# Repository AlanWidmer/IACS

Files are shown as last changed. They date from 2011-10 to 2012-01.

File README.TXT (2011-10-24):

The project is a fork of the shop.23b.org 'open access controller'. For the Jigsaw Renaissance space in the Inscape building we need to make some changes and additions.
The door controller will use the wireless ethernet infrastructure to pull a file that contains the list of valid keys from a server.

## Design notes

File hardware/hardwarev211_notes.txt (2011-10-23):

Open Access Control Notes
Updated 4/3/2011

Relay pins:
6,7,8,9

I2C for clock:
A4 (SDA)
A5 (SCL)
`
Analog pins (for alarm):
A0,A1,A2,A3

Reader inputs
Reader 1: 2,3
Reader 2: 4,5

Ethernet shield:
10,11,12,13

Changes sicne v2.00:
1.  Added additional TVS diode on the +5V rail
2.  Adjusted board layout so that insulator not needed under voltage regulator
3.  Tidied up silkscreen on top and bottom layers

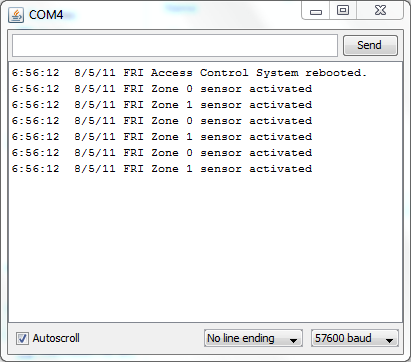
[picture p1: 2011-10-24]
Images/Running.PNG

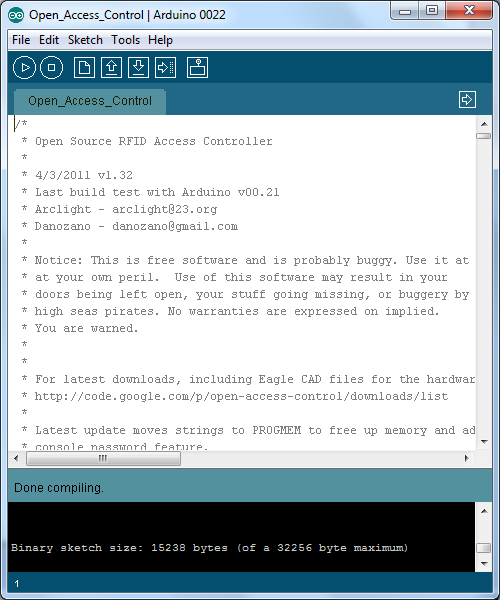
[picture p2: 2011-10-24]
Images/compiled.PNG

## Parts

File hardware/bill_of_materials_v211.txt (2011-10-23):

Partlist exported from H:/apps/eagle/projects/RFID/RFID_board_v200.sch at 1/20/2011 10:33:13 PM

Part    Value               Device               Package            Description                                                                                  DIGIKEY       MOUSER     
5VOUT                       W237-102             W237-102           WAGO SCREW CLAMP                                                                                           651-1935161
12VIN                       W237-102             W237-102           WAGO SCREW CLAMP                                                                                           651-1935161
12VOUTA                     W237-102             W237-102           WAGO SCREW CLAMP                                                                                           651-1935161
12VOUTB                     W237-102             W237-102           WAGO SCREW CLAMP                                                                                           651-1935161
BAT1                        BATTERY20PTH         BATTCOM_20MM_PTH   Battery Holders                                                                                            122-2420-GR
C1      100uF               CPOL-USE3.5-8        E3,5-8             POLARIZED CAPACITOR, American symbol                                                                                  
C2      0.1uF               C-US050-025X075      C050-025X075       CAPACITOR, American symbol                                                                                            
C3      330uF               CPOL-USE3.5-8        E3,5-8             POLARIZED CAPACITOR, American symbol                                                                                  
D1      1N5819              1N5819-B             DO41-7.6           1.0A SCHOTTKY BARRIER RECTIFIER                                                                                       
D2      15KE18A             15KE18A              DO201-15           TVS Diode, 18V                                                                                                         
D3	15KE6.8A	    15KE6.8A				    TVS Diode, 6.8V
D5      1N4004              1N4004               DO41-10            DIODE                                                                                                                 
D6      1N4004              1N4004               DO41-10            DIODE                                                                                                                 
D7      1N4004              1N4004               DO41-10            DIODE                                                                                                                 
D8      1N4004              1N4004               DO41-10            DIODE                                                                                                                 
D9      1N4004              1N4004               DO41-10            DIODE                                                                                                                 
D10     1N4004              1N4004               DO41-10            DIODE                                                                                                                 
D11     1N4004              1N4004               DO41-10            DIODE                                                                                                                 
D12     1N4004              1N4004               DO41-10            DIODE                                                                                                                 
D13     5A                  DIODE-P6-15          P6-15              DIODE                                                                                                                 
F1      2A                  5X20MMCLIP           SHK20Q             FUSE HOLDER Littelfuse 01110506H 5x20mm clips. Mouser part #576-01110506H                    F044-ND                  
F4      5A                  5X20MMCLIP           SHK20Q             FUSE HOLDER Littelfuse 01110506H 5x20mm clips. Mouser part #576-01110506H                    F044-ND                  
F6      2A                  5X20MMCLIP           SHK20Q             FUSE HOLDER Littelfuse 01110506H 5x20mm clips. Mouser part #576-01110506H                    F044-ND                  
F7      0.5A                5X20MMCLIP           SHK20Q             FUSE HOLDER Littelfuse 01110506H 5x20mm clips. Mouser part #576-01110506H                    F044-ND                  
IC1     DS1307              DS1307               DIL08              DS1307                                                                                       DS1307+-ND    700-DS1307 
IC5     ULN2003             ULN2003AN            DIL16              DRIVER ARRAY                                                                                                          
K0      GL5E-12V            ZNS5106              ZN5                Miniature Power PCB Relay SCHRACK                                                            Z1012-ND                 
K1      GL5E-12V            ZNS5106              ZN5                Miniature Power PCB Relay SCHRACK                                                            Z1012-ND                         
K2      GL5E-12V            ZNS5106              ZN5                Miniature Power PCB Relay SCHRACK                                                            Z1012-ND                 
K3      GL5E-12V            ZNS5106              ZN5                Miniature Power PCB Relay SCHRACK                                                            Z1012-ND                 
LED1    RED                 LED5MM               LED5MM             LED                                                                                                                   
LED2    RED                 LED5MM               LED5MM             LED                                                                                                                   
LED3    RED                 LED5MM               LED5MM             LED                                                                                                                   
LED4    RED                 LED5MM               LED5MM             LED                                                                                                                   
LED5    GRN                 LED5MM               LED5MM             LED                                                                                                                   
OK1     PS-2501             PS2501               DIL08              NEC PS OPTO COUPLER                                                                                                   
OK2     PS-2501             PS2501               DIL08              NEC PS OPTO COUPLER                                                                                                   
OK3     PS-2501             PS2501               DIL08              NEC PS OPTO COUPLER                                                                                                   
OK4     PS-2501             PS2501               DIL08              NEC PS OPTO COUPLER                                                                                                   
Q1      32Khz               CRYSTALTC26H         TC26H              CRYSTAL                                                                                                               
R1      2.2K                R-US_0207/10         0207/10            RESISTOR, American symbol                                                                                             
R2      S10K30              S10K30               S10K               VARISTOR  - 30V, 10mm package                                                                                         
R3      2.2K                R-US_0207/10         0207/10            RESISTOR, American symbol                                                                                             
R4      2.2K                R-US_0207/10         0207/10            RESISTOR, American symbol                                                                                             
R5      4.7K                R-US_0207/10         0207/10            RESISTOR, American symbol                                                                                             
R6      2.2K                R-US_0207/10         0207/10            RESISTOR, American symbol                                                                                             
R7      4.7K                R-US_0207/10         0207/10            RESISTOR, American symbol                                                                                             
R8      330                 R-US_0207/10         0207/10            RESISTOR, American symbol                                                                                             
R9      4.7K                R-US_0207/10         0207/10            RESISTOR, American symbol                                                                                             
R11     4.7K                R-US_0207/10         0207/10            RESISTOR, American symbol                                                                                             
R12     4.7K                R-US_0207/10         0207/10            RESISTOR, American symbol                                                                                             
R15     2.2K                R-US_0207/10         0207/10            RESISTOR, American symbol                                                                                             
R16     2.2K                R-US_0207/10         0207/10            RESISTOR, American symbol                                                                                             
R17     2.2K                R-US_0207/10         0207/10            RESISTOR, American symbol                                                                                             
R18     2.2K                R-US_0207/10         0207/10            RESISTOR, American symbol                                                                                             
R20     2.2K                R-US_0207/10         0207/10            RESISTOR, American symbol                                                                                             
R22     4.7K                R-US_0207/10         0207/10            RESISTOR, American symbol                                                                                             
R23     2.2K                R-US_0207/10         0207/10            RESISTOR, American symbol                                                                                             
R25     2.2K                R-US_0207/10         0207/10            RESISTOR, American symbol                                                                                             
R27     4.7K                R-US_0207/10         0207/10            RESISTOR, American symbol                                                                                             
R28     4.7K                R-US_0207/10         0207/10            RESISTOR, American symbol                                                                                             
R32     2.2K                R-US_0207/10         0207/10            RESISTOR, American symbol                                                                                             
R33     4.7K                R-US_0207/10         0207/10            RESISTOR, American symbol                                                                                             
R34     4.7K                R-US_0207/10         0207/10            RESISTOR, American symbol                                                                                             
READER1                     W237-102             W237-102           WAGO SCREW CLAMP                                                                                           651-1935161
READER2                     W237-102             W237-102           WAGO SCREW CLAMP                                                                                           651-1935161
RELAY0                      W237-103             W237-103           WAGO SCREW CLAMP                                                                                           651-1935174
RELAY1                      W237-103             W237-103           WAGO SCREW CLAMP                                                                                           651-1935174
RELAY2                      W237-103             W237-103           WAGO SCREW CLAMP                                                                                           651-1935174
RELAY3                      W237-103             W237-103           WAGO SCREW CLAMP                                                                                           651-1935174
SENS1                       W237-102             W237-102           WAGO SCREW CLAMP                                                                                           651-1935161
SENS2                       W237-102             W237-102           WAGO SCREW CLAMP                                                                                           651-1935161
U$1     LM2575              LM2575               TO220-5PIN-1       Fixed 5V Simple Switcher from National, staggered pins                                                                
U$2     330uH               PE-52647NLPE-52647NL PE-52647-NL        330uH, 1A Inductor from Pulse Engineering. Used with National Semiconductor Simple Switcher. 553-1558-5-ND            

Misc:
(1) ARDUINO_SHIELDLABEL 					    Arduino shield pins (2x6-pin, 2x8-pin). Purchase from Sparkfun.com or Adafruit.com
(1) BATT	 CR-2032 Battery
(1) HEATSINK Small TO220 heatsink, mounting screw+nut
(1) 5A 5x20mm fuse
(1) 500ma 5x20mm fuse
(2) 2A 5x20mm fuse
(3) 16-pin DIP socket (optional)
(1) 8-pin DIP socket (optional)

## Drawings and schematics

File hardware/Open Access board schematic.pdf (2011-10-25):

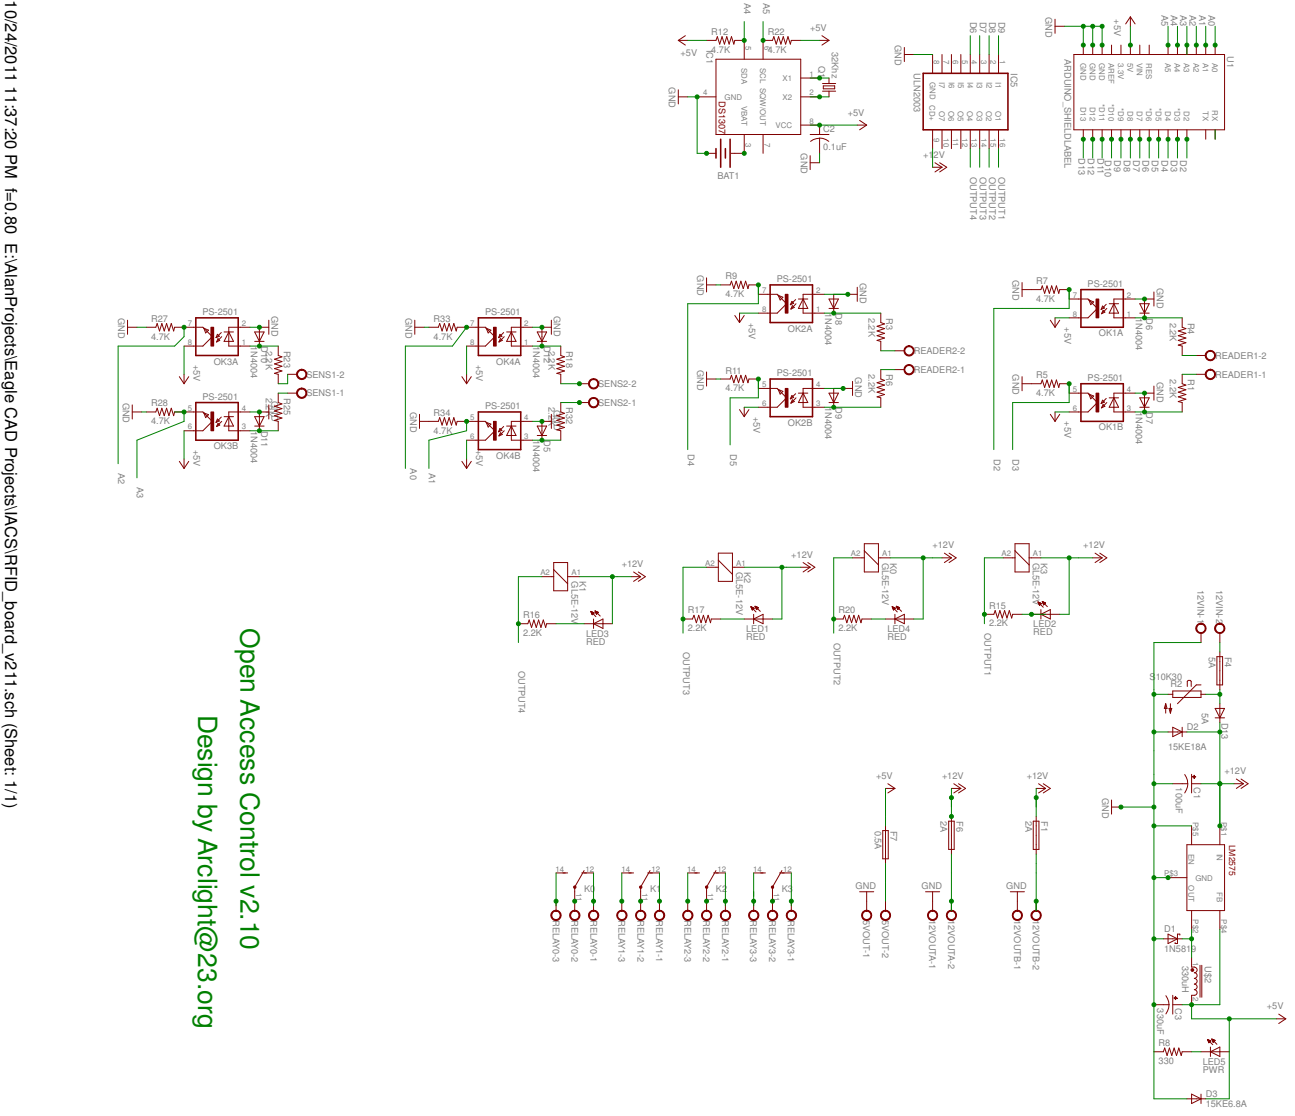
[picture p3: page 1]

10/24/2011 11:37:20 PM f=0.80 E:\AlanProjects\Eagle CAD Projects\IACS\RFID_board_v211.sch (Sheet: 1/1) PS-2501 PS-2501

Design by Arclight@23.org

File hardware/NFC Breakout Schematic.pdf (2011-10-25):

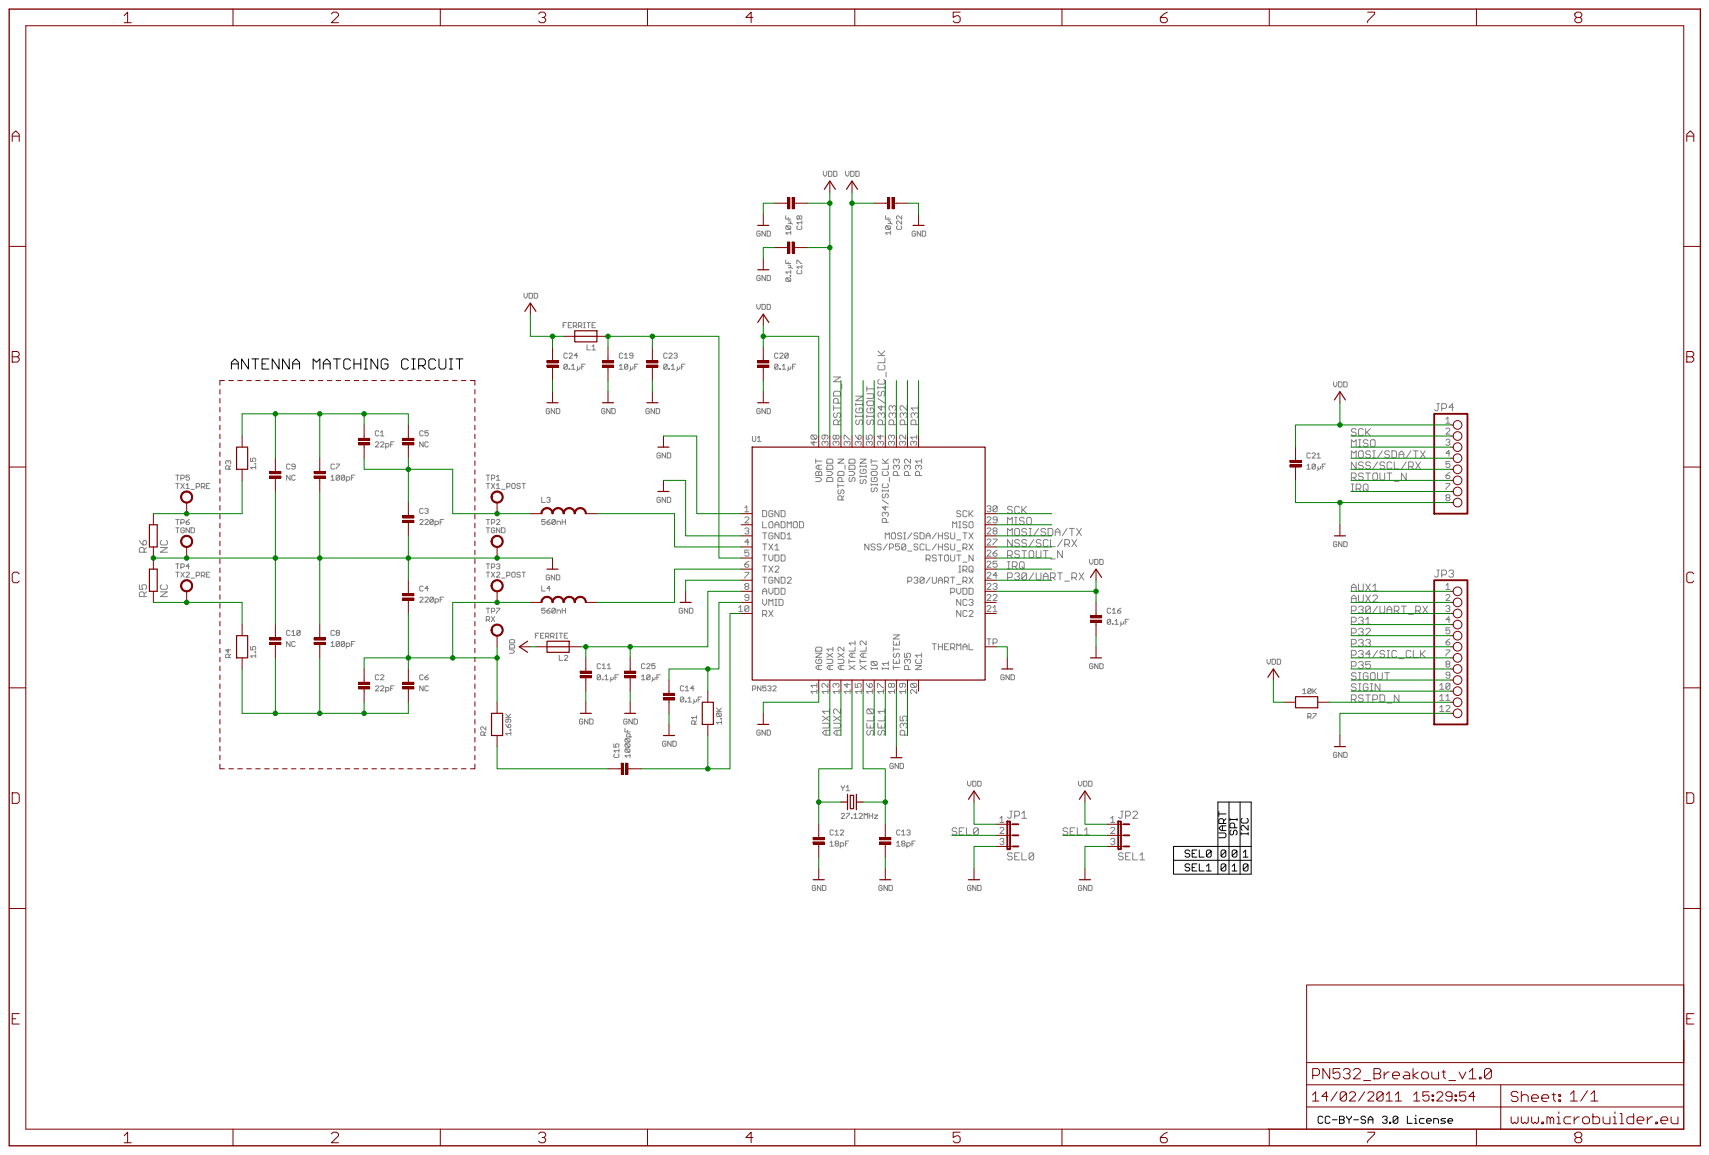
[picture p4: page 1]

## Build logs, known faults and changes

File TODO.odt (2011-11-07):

TODO list for Inscape Access Control System (IACS)

# SPI

The SPI library is not well suited to multiple devices on the bus. The Ethernet W5100 uses the library but the SD interface on the same board does not. For IACS we additionally have the NFC board which uses SPI for communication to the PN532 chip.

The changes to be made are:

Use the single global object SD as if it was a singleton object. Each device driver can use this so long as there is no multitasking.

The chip select line for each device must be managed by the device driver as the SPI driver has no real knowledge of chip selects (other than setting up the direction of the port pin for the Ethernet device.) There should be a private member variable that is set in the constructor so no other

The Ethernet device should setup the chip select port pin direction even though the SPI driver does this because it will be more consistant with the other two drivers.

The .begin member function should reprogram bitOrder, clockDivider, and dataMode. This is so that a system that only has one SPI device does not need the user to call the select() function and will maintain compatibility with the existing examples.

The SPI driver should have the software SPI code added and selected based on a compile time definition. This code is currently in the SD card code which is clearly the wrong place.

The program accessing all three devices will then have a structure like this:

// Instantiate driver objects

#define NFC_CS 5

#define W5100_CS 10

#define SD_CS 4

PN532 NFC(NFC_CS, ...);

W5100 Ethernet(W5100_CS, ...);

SD SDCARD(SD_CS, ...);

setup(){

nfc.begin();

Ethernet.begin();

SD.begin();

}

loop() {

NFC.select();

// do nfc stuff here;

Ethernet.select();

//do network stuff here

SD.select();

// do flash memory card stuff here

}

Need to figure out what the defaults are for SPI bitOrder, clockDivider, and dataMode because the Ethernet driver currently does not set them and if I set them to 0, 0, 0 it stops working.

Ethernet bit order is the default (MSBFirst) but NFC is LSBFirst. The default is MSBfirst so the NFC is setting it the wrong way for the ethernet W5100.

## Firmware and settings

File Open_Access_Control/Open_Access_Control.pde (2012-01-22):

/*
 * Open Source RFID Access Controller
 *
 * 4/3/2011 v1.32
 * Last build test with Arduino v00.21
 * Arclight - arclight@23.org
 * Danozano - danozano@gmail.com
 * Alan - alan@jigsawrenaissance.org
 *
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
 *
 * For latest downloads, including Eagle CAD files for the hardware, check out
 * http://code.google.com/p/open-access-control/downloads/list
 *
 * Latest update moves strings to PROGMEM to free up memory and adds a 
 * console password feature.
 * 
 *
 * This program interfaces the Arduino to RFID, PIN pad and all
 * other input devices using the Wiegand-26 Communications
 * Protocol. It is recommended that the keypad inputs be
 * opto-isolated in case a malicious user shorts out the 
 * input device.
 * Outputs go to a Darlington relay driver array for door hardware/etc control.
 * Analog inputs are used for alarm sensor monitoring.  These should be
 * isolated as well, since many sensors use +12V. Note that resistors of
 * different values can be used on each zone to detect shorting of the sensor
 * or wiring.
 *
 * Version 1.00+ of the hardware implements these features and uses the following pin 
 * assignments on a standard Arduino Duemilanova or Uno:
 *
 * Relay outputs on digital pins 6,7,8,9
 * DS1307 Real Time Clock (I2C):A4 (SDA), A5 (SCL)
 * Analog pins (for alarm):A0,A1,A2,A3 
 * Reader 1: pins 2,3
 * Reader 2: pins 4,5
 * Ethernet: pins 10,11,12,13 (Not connected to the board, reserved for the Ethernet shield)
 *
 * Quickstart tips: 
 * Set the console password(PRIVPASSWORD) value to a numeric DEC or HEX value.
 * Define the static user list by swiping a tag and copying the value received into the #define values shown below 
 * Compile and upload the code, then log in via serial console at 57600,8,N,1
 *
 */

/* TODO: The SPI interface from the PN532 library is not compatible with the SD card */
/* Replace both with calls to the SPI library */
/* TODO Put the readers into a class so it is easy to change the number of instantiated readers */
#include <Wire.h>         // Needed for I2C Connection to the DS1307 date/time chip
#include <EEPROM.h>       // Needed for saving to non-volatile memory on the Arduino.
#include <avr/pgmspace.h> // Allows data to be stored in FLASH instead of RAM

/*
#include <Ethernet.h>   // Ethernet stuff, comment out if not used.
#include <SPI.h>          
#include <Server.h>
#include <Client.h>
*/

#include <DS1307.h>       // DS1307 RTC Clock/Date/Time chip library
#include <WIEGAND26.h>    // Wiegand 26 reader format library
#include <PCATTACH.h>     // Pcint.h implementation, allows for >2 software interrupts.
#include <PN532.h>

/* Static user List - Implemented as an array for testing and access override 
 */                               

#define DEBUG 1                         // Set to 2 for display of raw tag numbers in log files, 1 for only denied, 0 for never.               

#define gonzo   0x1234                  // Name and badge number in HEX. We are not using checksums or site ID, just the whole
#define snake   1234                    // output string from the reader.
#define satan   12345678
const long  superUserList[] = { gonzo, snake, satan};  // Super user table (cannot be changed by software)

#define PRIVPASSWORD 0x1234             // Console "privileged mode" password

#define DOORDELAY 5000                  // How long to open door lock once access is granted. (2500 = 2.5s)
#define SENSORTHRESHOLD 100             // Analog sensor change that will trigger an alarm (0..255)

#define EEPROM_ALARM 0                  // EEPROM address to store alarm triggered state between reboots (0..511)
#define EEPROM_ALARMARMED 1             // EEPROM address to store alarm armed state between reboots
#define EEPROM_ALARMZONES 20            // Starting address to store "normal" analog values for alarm zone sensor reads.
#define KEYPADTIMEOUT 5000              // Timeout for pin pad entry. Users on keypads can enter commands after reader swipe.

#define EEPROM_FIRSTUSER 24
#define EEPROM_LASTUSER 1024
#define NUMUSERS  ((EEPROM_LASTUSER - EEPROM_FIRSTUSER)/5)  //Define number of internal users (200 for UNO/Duemillanova)


#define DOORPIN1 relayPins[0]           // Define the pin for electrified door 1 hardware
#define DOORPIN2 relayPins[2]           // Define the pin for electrified door 2 hardware
#define ALARMSTROBEPIN relayPins[3]     // Define the "non alarm: output pin. Can go to a strobe, small chime, etc
#define ALARMSIRENPIN  relayPins[1]     // Define the alarm siren pin. This should be a LOUD siren for alarm purposes.

#define SCK 13
#define MOSI 11
#define NFC_SS 5
#define MISO 12

// TODO find out from Arclight why the comments don't match the code
uint8_t reader1Pins[]={2,3};               // Reader 1 connected to pins 4,5
// TODO uint8_t reader2Pins[]= {4,5};              // Reader2 connected to pins 6,7

//uint8_t reader3Pins[]= {10,11};                // Reader3 connected to pins X,Y (Not implemented on v1.x and 2.x Access Control Board)

const uint8_t analogsensorPins[] = {0,1,2,3};    // Alarm Sensors connected to other analog pins
const uint8_t relayPins[]= {6,7,8,9};            // Relay output pins

bool door1Locked=true;                        // Keeps track of whether the doors are supposed to be locked right now
bool door2Locked=true;

unsigned long door1locktimer=0;               // Keep track of when door is supposed to be relocked
unsigned long door2locktimer=0;               // after access granted.

bool doorChime=false;                       // Keep track of when door chime last activated
bool doorClosed=false;                      // Keep track of when door last closed for exit delay

unsigned long alarmDelay=0;                    // Keep track of alarm delay. Used for "delayed activation" or level 2 alarm.
unsigned long alarmSirenTimer=0;               // Keep track of how long alarm has gone off


unsigned long consolefailTimer=0;               // Console password timer for failed logins
uint8_t consoleFail=0;
#define numUsers (sizeof(superUserList)/sizeof(long))                  //User access array size (used in later loops/etc)
#define NUMDOORS (sizeof(doorPin)/sizeof(uint8_t))
#define numAlarmPins (sizeof(analogsensorPins)/sizeof(uint8_t))

//Other global variables
uint8_t second, minute, hour, dayOfWeek, dayOfMonth, month, year;     // Global RTC clock variables. Can be set using DS1307.getDate function.

uint8_t alarmActivated = EEPROM.read(EEPROM_ALARM);                   // Read the last alarm state as saved in eeprom.
uint8_t alarmArmed = EEPROM.read(EEPROM_ALARMARMED);                  // Alarm level variable (0..5, 0==OFF) 

bool sensor[4]={false};                                         // Keep track of tripped sensors, do not log again until reset.
unsigned long sensorDelay[2]={0};                                  // Same as above, but sets a timer for 2 of them. Useful for logging
                                                                   // motion detector hits for "occupancy check" functions.

// Enable up to 3 door access readers.
volatile long reader1 = 0;
volatile int  reader1Count = 0;
volatile long reader2 = 0;
volatile int  reader2Count = 0;
int userMask1=0;
int userMask2=0;
bool keypadGranted=0;                                       // Variable that is set for authenticated users to use keypad after login
long nfcId;

volatile long reader3 = 0;                                   // Uncomment if using a third reader.
volatile int  reader3Count = 0;

unsigned long keypadTime = 0;                                  // Timeout counter for  reader with key pad
unsigned long keypadValue=0;


// Serial terminal buffer (needs to be global)
char inString[40]={0};                                         // Size of command buffer (<=128 for Arduino)
uint8_t inCount=0;
bool privmodeEnabled = false;                               // Switch for enabling "privileged" commands



/* Create an instance of the various C++ libraries we are using.
 */

DS1307 ds1307;        // RTC Instance
WIEGAND26 wiegand26;  // Wiegand26 (RFID reader serial protocol) library
PCATTACH pcattach;    // Software interrupt library
PN532 nfc(SCK, MISO, MOSI, NFC_SS);

/* Set up some strings that will live in flash instead of memory. This saves our precious 2k of
 * RAM for something else.
*/

const prog_uchar rebootMessage[]          PROGMEM  = {"Access Control System rebooted."};

const prog_uchar doorChimeMessage[]       PROGMEM  = {"Front Door opened."};
const prog_uchar doorslockedMessage[]     PROGMEM  = {"All Doors relocked"};
const prog_uchar alarmtrainMessage[]      PROGMEM  = {"Alarm Training performed."};
const prog_uchar privsdeniedMessage[]     PROGMEM  = {"Access Denied. Privileged mode is not enabled."};
const prog_uchar privsenabledMessage[]    PROGMEM  = {"Privileged mode enabled."};
const prog_uchar privsdisabledMessage[]   PROGMEM  = {"Privileged mode disabled."};
const prog_uchar privsAttemptsMessage[]   PROGMEM  = {"Too many failed attempts. Try again later."};

const prog_uchar consolehelpMessage1[]    PROGMEM  = {"Valid commands are:"};
const prog_uchar consolehelpMessage2[]    PROGMEM  = {"(d)ate, (s)show user, (m)odify user <num>  <usermask> <tagnumber>"};
const prog_uchar consolehelpMessage3[]    PROGMEM  = {"(a)ll user dump,(r)emove_user <num>,(o)open door <num>"};
const prog_uchar consolehelpMessage4[]    PROGMEM  = {"(u)nlock all doors,(l)lock all doors"};
const prog_uchar consolehelpMessage5[]    PROGMEM  = {"(1)disarm_alarm, (2)arm_alarm,(3)train_alarm (9)show_status"};
const prog_uchar consolehelpMessage6[]    PROGMEM  = {"(e)nable <password> - enable or disable privileged mode"};
const prog_uchar consoledefaultMessage[]  PROGMEM  = {"Invalid command. Press '?' for help."};

const prog_uchar statusMessage1[]         PROGMEM  = {"Alarm armed state (1=armed):"};
const prog_uchar statusMessage2[]         PROGMEM  = {"Alarm siren state (1=activated):"};
const prog_uchar statusMessage3[]         PROGMEM  = {"Front door open state (0=closed):"};
const prog_uchar statusMessage4[]         PROGMEM  = {"Roll up door open state (0=closed):"};     
const prog_uchar statusMessage5[]         PROGMEM  = {"Door 1 unlocked state(1=locked):"};                   
const prog_uchar statusMessage6[]         PROGMEM  = {"Door 2 unlocked state(1=locked):"}; 




void setup(){           // Runs once at Arduino boot-up


    Wire.begin();   // start Wire library as I2C-Bus Master

  /* Attach pin change interrupt service routines from the Wiegand RFID readers
   */
  pcattach.PCattachInterrupt(reader1Pins[0], callReader1Zero, CHANGE); 
  pcattach.PCattachInterrupt(reader1Pins[1], callReader1One,  CHANGE);  
  // pcattach.PCattachInterrupt(reader2Pins[1], callReader2One,  CHANGE);
  // pcattach.PCattachInterrupt(reader2Pins[0], callReader2Zero, CHANGE);

  //Clear and initialize readers
  wiegand26.initReaderOne(); //Set up Reader 1 and clear buffers.
  // TODO wiegand26.initReaderTwo(); 
  nfc.begin();
  uint32_t versiondata = nfc.getFirmwareVersion();


  //Initialize output relays

  for(uint8_t i=0; i<4; i++){        
    pinMode(relayPins[i], OUTPUT);                                                      
    digitalWrite(relayPins[i], LOW);                  // Sets the relay outputs to LOW (relays off)
  }


 //ds1307.setDateDs1307(0,37,23,6,25,2,11);         
  /*  Sets the date/time (needed once at commissioning)
   
   uint8_t second,        // 0-59
   uint8_t minute,        // 0-59
   uint8_t hour,          // 1-23
   uint8_t dayOfWeek,     // 1-7
   uint8_t dayOfMonth,    // 1-28/29/30/31
   uint8_t month,         // 1-12
   uint8_t year);          // 0-99
   */



  Serial.begin(57600);	               	       // Set up Serial output at 8,N,1,57600bps
  logReboot();
  chirpAlarm(1);                               // Chirp the alarm to show system ready.

  if (versiondata == 0) {
      Serial.println("Didn't find PN53x board");
  }
  else {
    // Got ok data, print it out!
    Serial.print("Found chip PN5"); Serial.println((versiondata>>24) & 0xFF, HEX);
    Serial.print("Firmware ver. "); Serial.print((versiondata>>16) & 0xFF, DEC);
    Serial.print('.'); Serial.println((versiondata>>8) & 0xFF, DEC);
    Serial.print("Supports "); Serial.println(versiondata & 0xFF, HEX);
  }
//  hardwareTest(100);                         // IO Pin testing routing (use to check your inputs with hi/lo +(5-12V) sources)
                                               // Also checks relays

  // configure board to read RFID tags and cards
  nfc.SAMConfig();


}
void loop()                                     // Main branch, runs over and over again
{                         

readCommand();                                 // Check for commands entered at serial console

  
  /* Check if doors are supposed to be locked and lock/unlock them 
   * if needed. Uses global variables that can be set in other functions.
   */

  if(((millis() - door1locktimer) >= DOORDELAY) && (door1locktimer !=0))
  { 
    if(door1Locked==true){
     doorLock(1);
     door1locktimer=0;    }

    else {                        
      doorUnlock(1); 
      door1locktimer=0;
                        }                         
   }

  

 if(((millis() - door2locktimer) >= DOORDELAY) && (door2locktimer !=0))
  { 
    if(door2Locked==true) {
     doorLock(2); 
     door2locktimer=0;
                          }
   
    else {
     doorUnlock(2); 
     door2locktimer=0;
                         }   
  }   

  /*  Set optional "failsafe" time to lock up every night.
  */

  ds1307.getDateDs1307(&second, &minute, &hour, &dayOfWeek, &dayOfMonth, &month, &year);   // Get the current date/time

  if(hour==23 && minute==59 && door1Locked==false){
         doorLock(1);
// TODO Let Arclight know that the line below used to read door1Locked == true;
         door1Locked = true;
         Serial.println("Door 1 locked for 2359 bed time.");
  }



  // Notes: RFID polling is interrupt driven, just test for the reader1Count value to climb to the bit length of the key
  // change reader1Count & reader1 et. al. to arrays for loop handling of multiple reader output events
  // later change them for interrupt handling as well!
  // currently hardcoded for a single reader unit

  /* This code checks a reader with a 26-bit keycard input. Use the second routine for readers with keypads.  
   * A 5-second window for commands is opened after each successful key access read.
   */

  if(reader1Count >= 26){                           //  When tag presented to reader1 (No keypad on this reader)
    logTagPresent(reader1,1);                       //  write log entry to serial port
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

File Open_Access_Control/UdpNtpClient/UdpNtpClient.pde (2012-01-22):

/*

 Udp NTP Client
 
 Get the time from a Network Time Protocol (NTP) time server
 Demonstrates use of UDP sendPacket and ReceivePacket 
 For more on NTP time servers and the messages needed to communicate with them, 
 see http://en.wikipedia.org/wiki/Network_Time_Protocol
 
 created 4 Sep 2010 
 by Michael Margolis
 modified 17 Sep 2010
 by Tom Igoe
 
 This code is in the public domain.

 */

#include <SPI.h>         
#include <Ethernet.h>
#include <Udp.h>


#include <PN532.h>

// Enter a MAC address and IP address for your controller below.
// The IP address will be dependent on your local network:
uint8_t mac[] = {  
  0x90, 0xA2, 0xDA, 0x00, 0x3F, 0x78 };
uint8_t ip[] = { 
  10,0,1,15 };


unsigned int localPort = 8888;      // local port to listen for UDP packets

uint8_t timeServer[] = { 
  216, 171, 124, 36}; // NTP server

const int NTP_PACKET_SIZE= 48; // NTP time stamp is in the first 48 uint8_ts of the message

uint8_t packetBuffer[ NTP_PACKET_SIZE]; //buffer to hold incoming and outgoing packets 

#define SCK 13
#define MOSI 11
#define NFC_SS 5
#define MISO 12

PN532 nfc(SCK, MISO, MOSI, NFC_SS);

void setup() 
{
  Serial.begin(57600);
  Serial.println("Setup starting");
  pinMode(NFC_SS, OUTPUT);
  digitalWrite(NFC_SS, HIGH); //deselect

  // TODO this is just temp until nfc.begin works
  //pinMode(NFC_SS, OUTPUT);
  //digitalWrite(NFC_SS, HIGH); //deselect
  // start Ethernet and UDP
  Ethernet.begin(mac,ip);
  Serial.println("Ethernet begin complete");
  Udp.begin(localPort);
  Serial.println("Udp begin complete");

  //nfc.begin();
  Serial.println("NFC begin complete");

  Serial.println("Setup complete");

}

void loop()
{
  Serial.println("Start loop");
  // Ethernet.select();
  Serial.println("Ethernet selected");
  sendNTPpacket(timeServer); // send an NTP packet to a time server
  Serial.println("Packet Sent");

    // wait to see if a reply is available
  delay(1000);
  if ( Udp.available() ) {  
      Serial.println("UDP Packet received");
      Udp.readPacket(packetBuffer,NTP_PACKET_SIZE);  // read the packet into the buffer

    //the timestamp starts at uint8_t 40 of the received packet and is four uint8_ts,
    // or two words, long. First, extract the two words:

    unsigned long highWord = word(packetBuffer[40], packetBuffer[41]);
    unsigned long lowWord = word(packetBuffer[42], packetBuffer[43]);  
    // combine the four uint8_ts (two words) into a long integer
    // this is NTP time (seconds since Jan 1 1900):
    unsigned long secsSince1900 = highWord << 16 | lowWord;  
    Serial.print("Seconds since Jan 1 1900 = " );
    Serial.println(secsSince1900);               

    // now convert NTP time into everyday time:
    Serial.print("Unix time = ");
    // Unix time starts on Jan 1 1970. In seconds, that's 2208988800:
    const unsigned long seventyYears = 2208988800UL;     
    // subtract seventy years:
    unsigned long epoch = secsSince1900 - seventyYears;  
    // print Unix time:
    Serial.println(epoch);                               


    // print the hour, minute and second:
    Serial.print("The UTC time is ");       // UTC is the time at Greenwich Meridian (GMT)
    Serial.print((epoch  % 86400L) / 3600); // print the hour (86400 equals secs per day)
    Serial.print(':');  
    Serial.print((epoch  % 3600) / 60); // print the minute (3600 equals secs per minute)
    Serial.print(':'); 
    Serial.println(epoch %60); // print the second
  }
  else
  {
    Serial.println("No reply from time server");
  }
  // wait thirty seconds before asking for the time again
  delay(30000); 
}

// send an NTP request to the time server at the given address 
unsigned long sendNTPpacket(uint8_t *address)
{
  // set all uint8_ts in the buffer to 0
  memset(packetBuffer, 0, NTP_PACKET_SIZE); 
  // Initialize values needed to form NTP request
  // (see URL above for details on the packets)
  packetBuffer[0] = 0b11100011;   // LI, Version, Mode
  packetBuffer[1] = 0;     // Stratum, or type of clock
  packetBuffer[2] = 6;     // Polling Interval
  packetBuffer[3] = 0xEC;  // Peer Clock Precision
  // 8 uint8_ts of zero for Root Delay & Root Dispersion
  packetBuffer[12]  = 49; 
  packetBuffer[13]  = 0x4E;
  packetBuffer[14]  = 49;
  packetBuffer[15]  = 52;

  // all NTP fields have been given values, now
  // you can send a packet requesting a timestamp: 		   
  Udp.sendPacket( packetBuffer,NTP_PACKET_SIZE,  address, 123); //NTP requests are to port 123
}

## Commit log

2011-10-23 first commit based on shop.23b.org Open Access Controller.
    [RFID_board_v211.brd, RFID_board_v211.sch, power_board_ups_only.brd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]
2011-10-24 Images of the Arduino IDE working
2011-10-24 Adding the Arduino code from shop.23b.org
2011-10-24 Files for using Eclipse as the IDE instead of the Arduino IDE.
2011-10-25 Schematics in PDF format for convenience.
2011-10-26 Removed Reader2 because it uses the chip select line for the NFC chip. Now the NFC board is detected.
2011-10-30 Added the libraries that I think I need to modify in order to get the PN532 to use standard SPI lib. Modified PN532 lib to start the migration to using SPI lib.
2011-10-31 Version that works using the SPI library with the PN532 NFC reader. Integrated the NFC reader with the main Open Access Controller code to open doors.
2011-11-02 Trying to integrate the Ethernet board with the rest of the project.
2011-11-07 Modified the Ethernet, SD, and PN532 libraries to add a method 'select' to each to allow multiple devices to share the SPI bus. Still hangs if the PN532 is not attached to the system.
2012-01-15 Trying to prevent the Ethernet from hanging when the NFC is enabled. Not having much success however.
    [UdpNtpClient.pde]
2012-01-16 Adding datasheet for the micro used on the Arduino Uno board as the USB controller. Modified the PN532 select method so that it does not leave the chip selected.
2012-01-22 Changes made to support Arduino V1.0. Some types have changed, and methods on the 'wire' object were renamed. Significant changes have been made to the Ethernet library for V1.0 so I backed my versio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
